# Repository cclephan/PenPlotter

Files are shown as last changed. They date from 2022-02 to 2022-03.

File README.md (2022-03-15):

# Pen Plotter
## Date Updated: March 15, 2022
## Christian Clephan, Kyle McGrath
### Introduction

Our device was a 2.5 axis pen plotter, capable of taking in HPGL files as input and drawing on a piece of paper as the output. For our device we used polar coordinates. A radial arm moving around a hub was used to create the changes in angle, and the pen was moved radially using a rail system with a belt to provide the radial motion. The remaining 0.5 axis is the moving of the pen up and down. 

The device was intended to be used by its two creators: Christian Clephan and Kyle McGrath to demonstrate their mechatronics knowledge in the Term Project. Our goal was to create a robot which could draw anything, which we were able to accomplish by drawing some parallel lines, arcs, and scripples in the formation of a rectangle.

### Hardware Design Overview
Our Pen Plotter has two degrees of freedom controlled by two Pittperson DC motors and the half degree of freedom controlled by 1 servo motor. The servo motor controls the up and down motion of the pen by swinging in an arc downwards and perpendicular to the page, or upwards and parallel (not touching the page). One of the DC motors controls the radial motion of the pen plotter by spinning a timing belt, while housed on the rotational base. The timing belt fits around the motor gear and pulley wheel on the opposite side, which moves a carriage holding the servo motor and pen. The carriage rests on two metal rods which allow it to freely move in the radial direction. The angular direction is controlled by the other DC motor spinning the base holding the plotter. A wheel was attached to the other end of the plotter to allow for rotation as the motor spun the entire system. The spinning base, wheel, carriage, and radial motor housing were all 3D printed. Other materials such as the rods, pulley wheel, and fasteners were found in the lab scrap bin, while the timing belt was purchased from McMaster-Carr. Detailed drawings and CAD models of the hardware can be found at https://github.com/cclephan/PenPlotter/tree/main/PenPlotterModel.

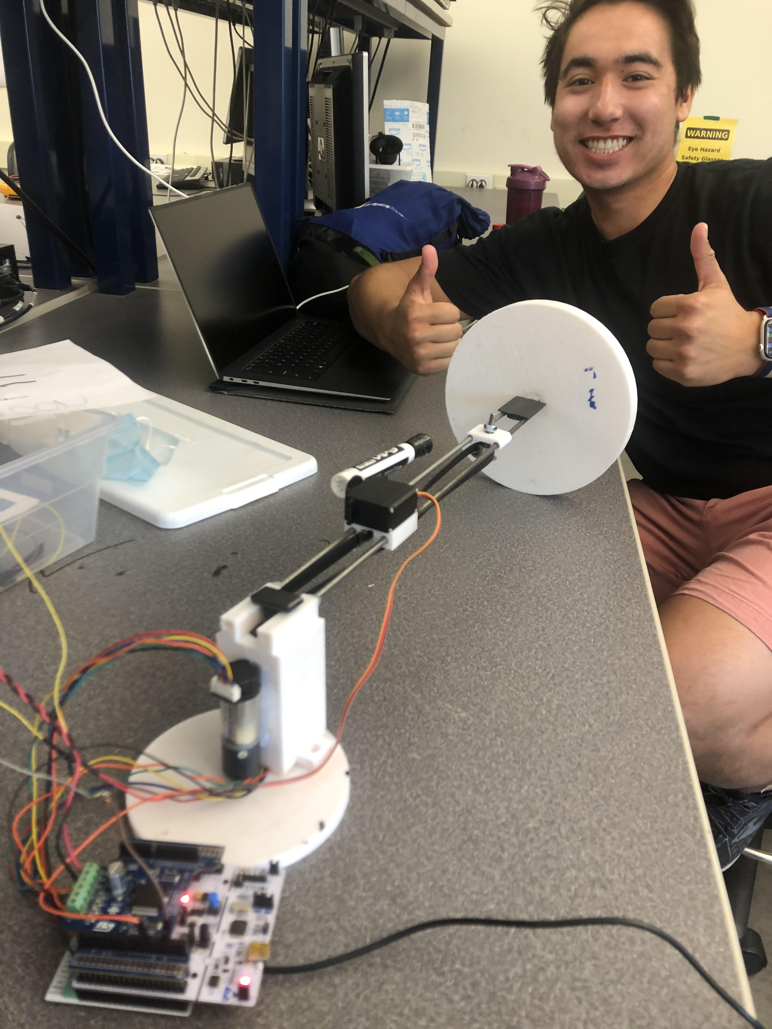
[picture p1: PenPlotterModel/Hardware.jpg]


Figure 1: Pen Plotter Hardware

### Software Design Overiew
Link to Doxygen for futher software design details: https://cclephan.github.io/PenPlotter/

The software consisted of utilizing several of our old files used in previous ME 405 labs as well as some new files to manage the HPGL processing. 

The files that were reused from previous labs were the Closed Loop Controller File, the Motor Driver File, and the Encoder Reader File. 

The parsing file would open the respective HPGL file and convert the HPGL coordinates into two rotational commands that are inputted into the closed loop controller file. HPGL coordiantes were provided in X and Y coordinates, these were converted to Polar Coordiantes using Trigonometry. The radial coordinate was then converted to a second theta coordinate for the motor driving the radial motion. 

The servo driver file was also new and included creating a timer, timer channel, and two functions which applied a PWM signal turning the servo motor so the pen is either up or down.

Our Task Diagram for the whole system can be seen in the Doxygen page. Some of the organization for the tasks have changed since the proposal, but this was due to hardware and time limitations. 

### Results
Our system came close to drawing what was inputted from the HPGL file, but there were still several shortcomings. Our most successful attempt was an attempt to draw two parallel lines, a video of which can be seen below. 

We tested our system by providing HPGL inputs and printing the respective commands provided to the motors. We then performed hand calculations to confirm that the commands provided to the motors match what we wanted to do. Initially we noticed that the commands that were provided to the motors did not match the hand calculations that we performed. We believed this was due to our use of Queues as we were saving our commands as integers instead of floats. We changed this and the inputs to the motors more closely followed desired results. 

The first HPGL file that we tested with our system was a straight line that was drawn in Inkscape and exported as an HPGL. One of earlier tests with drawing two straight lines can be seen here: https://youtu.be/u9vNNVAs_34. After taking some time to modify the speed of each motor and the period associated with each task, we eventually were able to draw two parallel lines. The video of drawing two parallel lines can be seen here: https://youtube.com/shorts/n7fFq1dV0Q4?feature=share. Some of our later tests that were unsuccessful were attempts to draw rectangles or circles. A failed rectangle attempt can be seen here: https://youtu.be/5r2_hMjXv8Q. We believe our system could have failed these tests because we did not interpolate between points which could have allowed for more defined motion between the points. We also struggled with finding a good condition statement to move to the next setpoint value once the motor has reached it's desired point. We tried to use a condition to see if the encoder position was close to the setpoint value, but it was hard to tune the controller for that condition, especially with the low resolution in our hardware design.

### What we learned
What worked well for this pen plotter was obtaining the hardware we needed and creating models that could be easily 3D printed and assembled. We noticed other groups struggled obtaining and purchasing materials, while most of our parts could be printed or found in the scrap bin. We were also able to complete tests to see how our motors moved the system around to ensure the hardware functioned as intended in the design. However, from this project we learned the importance of testing our code early and often. We made the mistake of believing the software portion of our project wouldn't be too complicated as we planned to reuse several files from older projects. We ran into some difficulty getting all the commands from the HPGL file to read as sometimes commands would get skipped over. We eventually learned this was likely due to either calling queue.read() twice as well as cotask running tasks either too quick or slow. There were other errors that we were unable to fix and from this we learned to not underestimate how long the software portion of a project will take. We also learned the importance of designing for as much resolution as possible in the hardware design, so controlling the motors in software would be much easier. Our rotational motor only had 1/4 revolution of a turn in resolution, which made positional control for complex shapes practically impossible. Sticking to a direct drive shaft attached to a smaller wheel would have been a much smarter choice as shown in the original example. 

Another thing we learned is the importance of using states in our code. We believed it would be easier to create code that works first and then implement the states after we had code that worked. In the end our code did not work as expected and we decided it was time to update the code to utilize states. We quickly saw that by using states, readability of the code improved significantly, and we were able to easily spot errors that we had missed. 

In the future we would recommend investigating interpolating the HPGL commands so there isn't as much noise. We would also recommend using direct drive for spinning a small wheel, therefore there is more resolution for position control. Finally, implementing finite states machines for each task early on would improve overall code readability and allow for quick code diagnosing. 

### Additional files 
Detailed CAD be found at: https://github.com/cclephan/PenPlotter/tree/main/PenPlotterModel

Two Line Video Attempt 1: https://youtu.be/u9vNNVAs_34

Two Line Video Succesful: https://youtube.com/shorts/n7fFq1dV0Q4?feature=share

Rectangle Video: https://youtu.be/5r2_hMjXv8Q

# Pen Plotter Proposal
## Date Updated: Feb 17, 2022 
## Christian Clephan, Kyle McGrath
### Description

Our proposed design will utilize a radial arm rotating around a hub. In the top right corner of the piece of paper will be a 3D rotating hub 
driven by a Pittperson Gearmotor. The gearmotor will provide torque to our radial arm which will consist of a rail system on which a flat bracket carrying the pen is mounted. The rail system will consist of metal tubes that we hope to find around the Aero Hanger and will be supported by 3D printed brackets (translational hub). The pen carrying bracket will be moved translationally by a belt. The belt will be obtained from McMaster-Carr and it will also be driven by a Pittperson Gearmotor. At the end of the rail system, we will mount a wheel in order to allow for free rotation of the system. At the end of the translational belt system there will be a platform to hold a gear, and on the other side a rod connecting to the free moving wheel. The wheel will likely be a hobby wheel for RC cars that we will obtain from Zacsters, or 3D printing could be an option. The pen carrier will be raised and lowered using an SG90 servo obtained from Zacsters. All parts with complex geometry or of small size will likely be 3D printed at Mustang 60. 

For our rail system, we want the rails to extend past the diameter of the paper in order to prevent the wheel from disrupting or damaging the paper. The rails will provide a fixed length between the motor and the wheel while also allowing the pen to move freely back and forth. All components, assembly, and drawing can be found in PenPlotterModel folder of this repository. Below is an drawing of our assembly with some dimensions (belt is not pictured, but would run between two translational gears).

One possible concern with our design is if the provided Pittperson Gearmotors can provide enough torque to drive the radial arm rails. Another concern of ours is implementing the rails to drive the pen radial motion as this is something we are both inexperienced with. 

Table 1. Bill of Materials

| Qty. | Part | Source | Est. Cost |
|:----:|:---|:---|:---:|
|  2 | Pittperson Gearmotors | ME405 Tub | - |
|  1 | Nucleo with Shoe | ME405 Tub | - |
|  1 | Purple Sharpie | Home supply | - |
|  1 | SG90 Servo | Zacsters | $1.50 |
|  3 | Metal Rods | Aero Hanger Trash | - |
|  1 | 3D Printed Translation Hub | Mustang 60 | - |
|  1 | RC Hobby Wheel | Zacsters | $3.00 |
|  1 | Belt | McMaster-Carr |  $10.43 |
|  1 | 3D Printed Pen Holder | Mustang 60 | - |
|  1 | Rotation Hub | Mustang 60 | - |
|  1 | Gear/Platform for Translation | Mustang 60 | - |

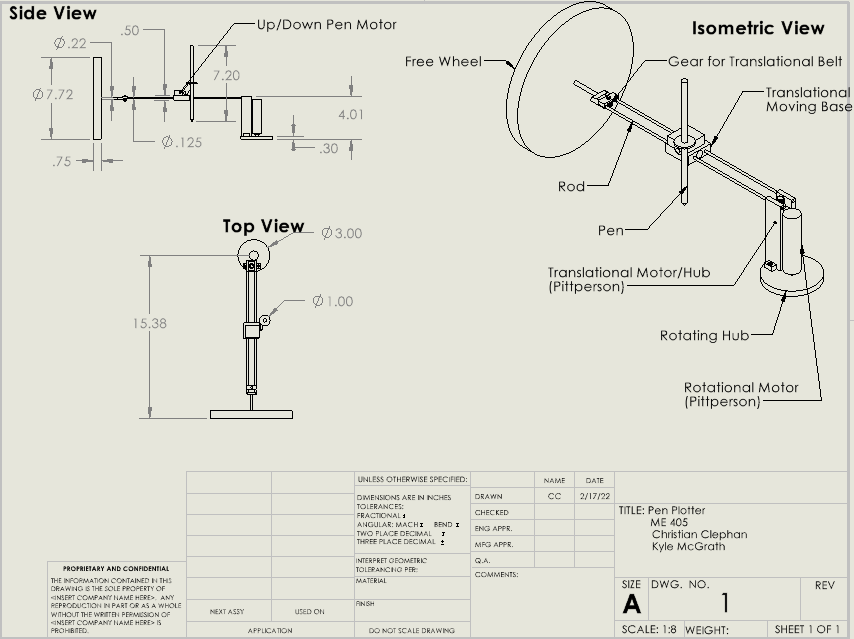
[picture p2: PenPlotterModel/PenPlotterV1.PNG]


Figure 1. Detailed Drawing of Pen Plotter Assembly

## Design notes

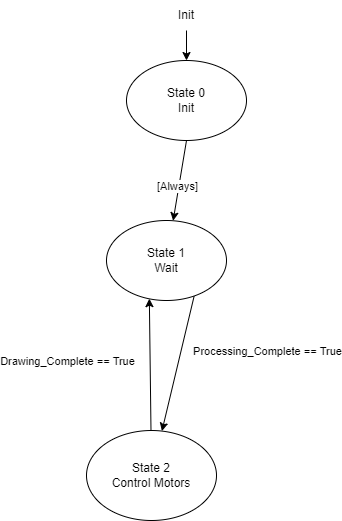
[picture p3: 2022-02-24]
docs/Controller_Task.png

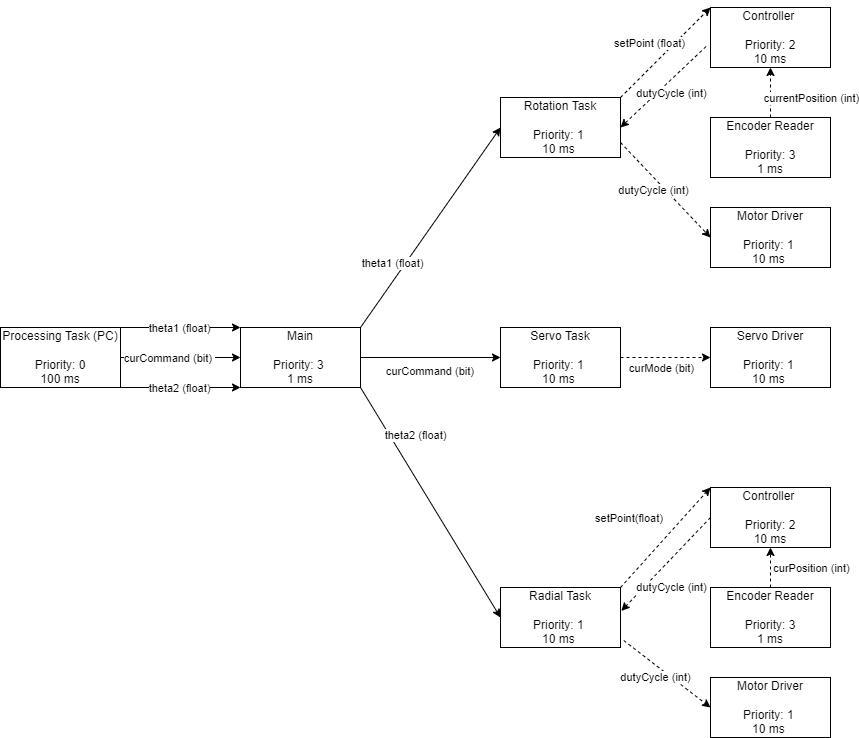
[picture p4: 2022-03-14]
docs/UpdatedTaskDiagram.png

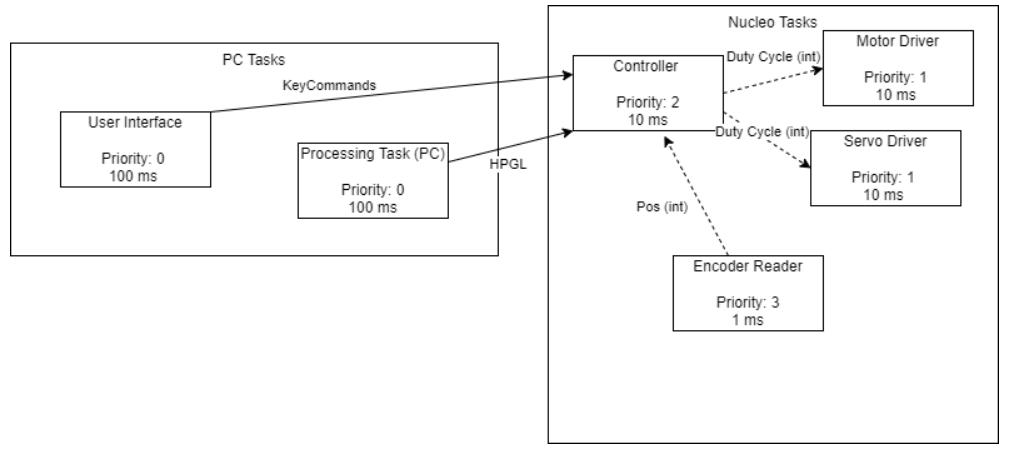
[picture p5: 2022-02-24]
docs/TaskDiagram.png

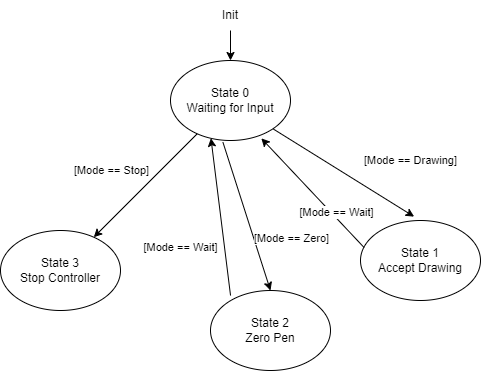
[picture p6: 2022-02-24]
docs/UI_Task.png

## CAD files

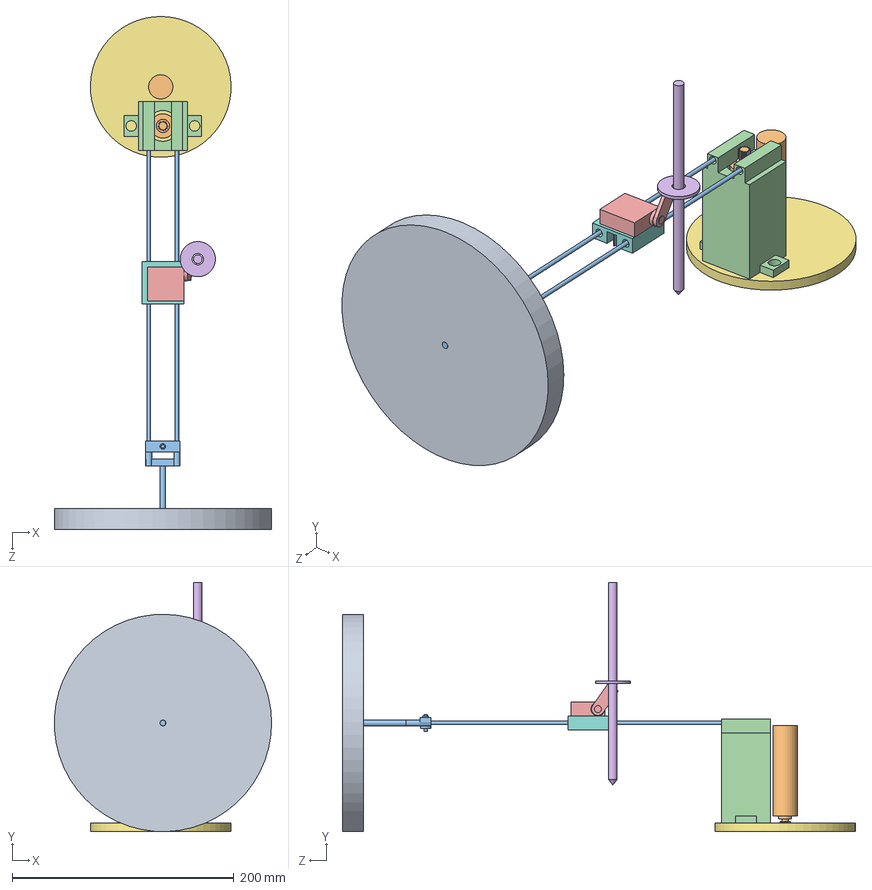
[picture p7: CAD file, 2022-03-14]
PenPlotterModel/Proto Pen Plotter.SLDASM
196.0 x 224.9 x 462.9 mm
Free Spinning Wheel
Pittman Motor x 2
Rod
Translational Motor Hub
2941 Mini Motor
Pencil Holder
Rotation Hub
Translational Moving Base

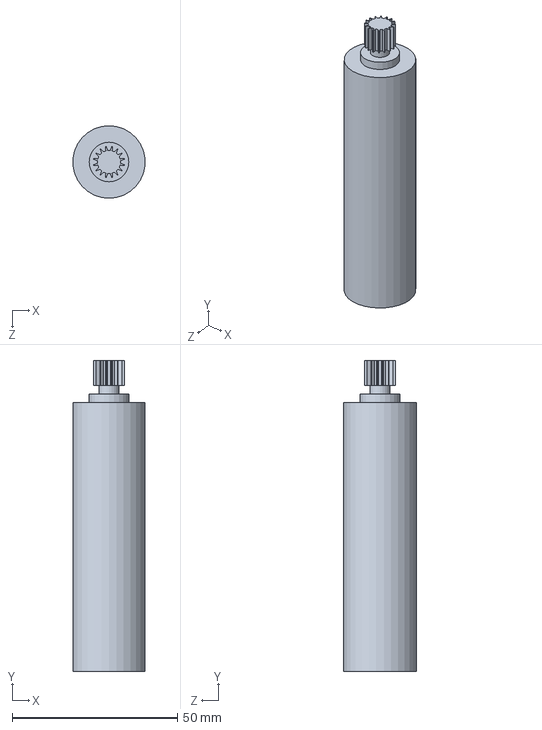
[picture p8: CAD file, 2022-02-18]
PenPlotterModel/Pittman Motor.SLDPRT
21.9 x 94.2 x 22.0 mm

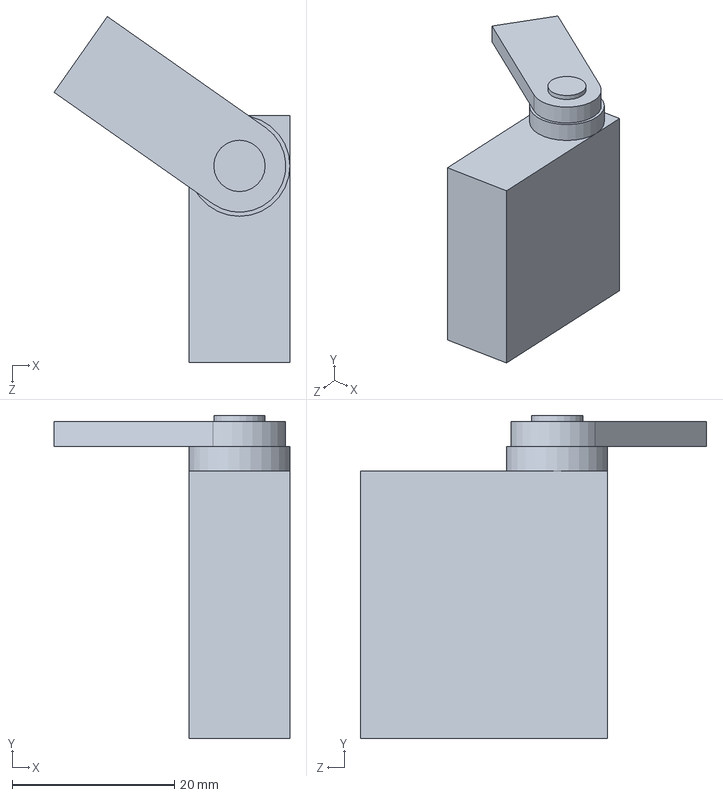
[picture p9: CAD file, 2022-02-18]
PenPlotterModel/2941 Mini Motor.SLDPRT
29.1 x 39.9 x 42.7 mm

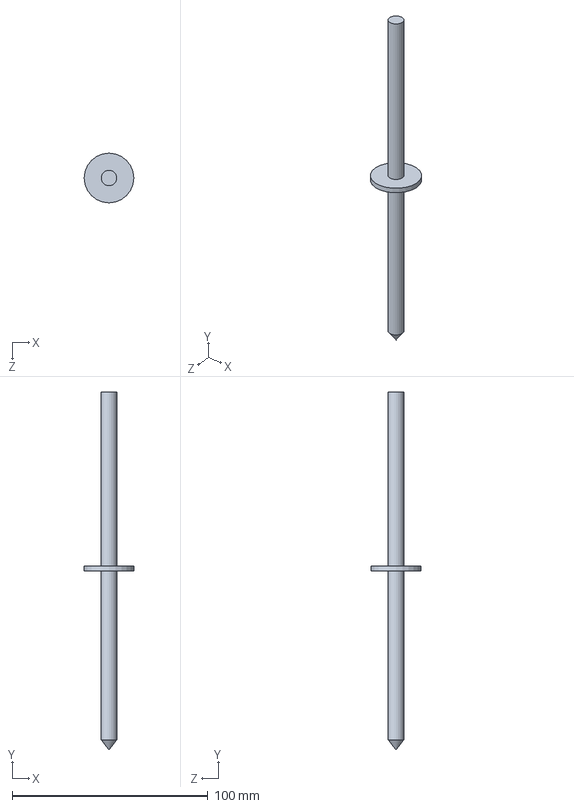
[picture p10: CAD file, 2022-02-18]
PenPlotterModel/Pencil Holder.SLDPRT
25.4 x 183.0 x 25.4 mm

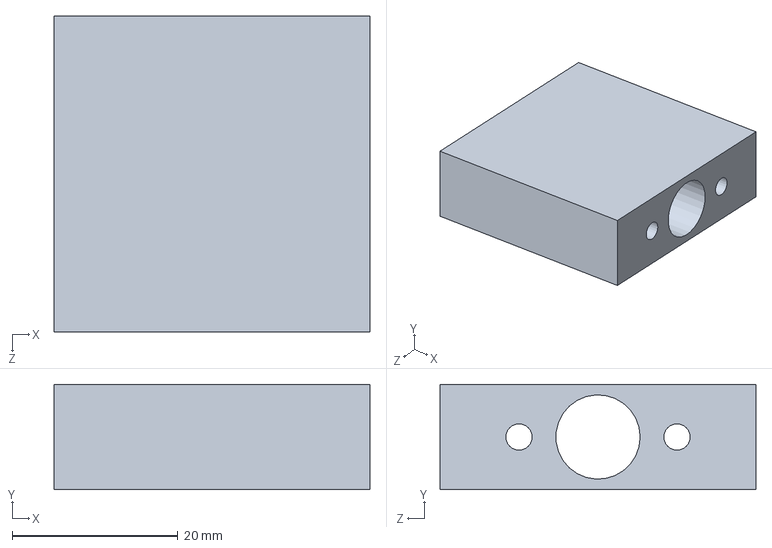
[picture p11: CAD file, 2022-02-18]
PenPlotterModel/Translational Moving Base.SLDPRT
38.1 x 12.7 x 38.1 mm

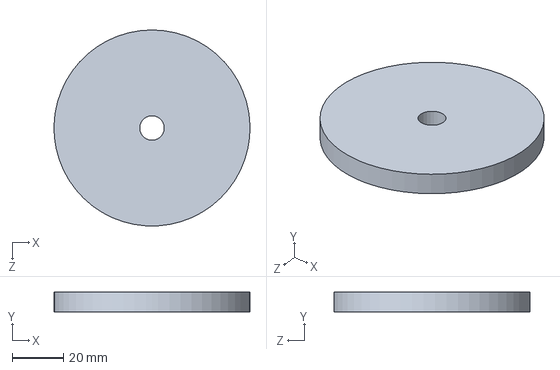
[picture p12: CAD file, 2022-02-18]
PenPlotterModel/Rotation Hub.SLDPRT
76.2 x 7.62 x 76.2 mm

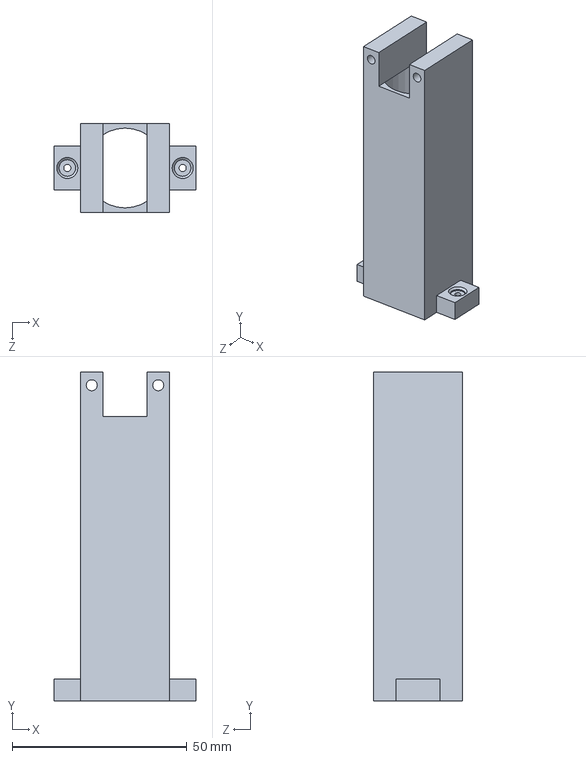
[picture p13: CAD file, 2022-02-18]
PenPlotterModel/Translational Motor Hub.SLDPRT
40.6 x 94.2 x 25.4 mm

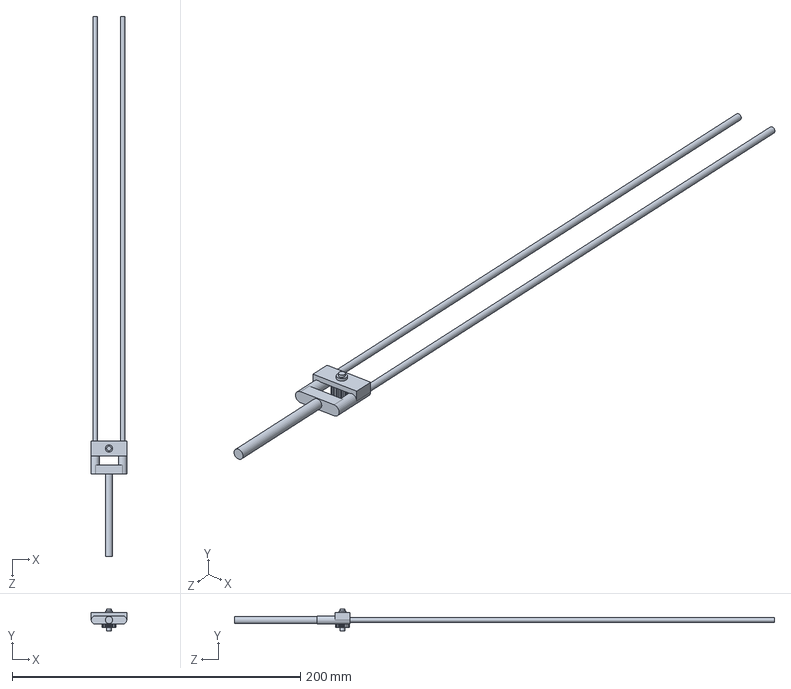
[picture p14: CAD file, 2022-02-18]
PenPlotterModel/Rod.SLDPRT
24.7 x 15.2 x 374.6 mm

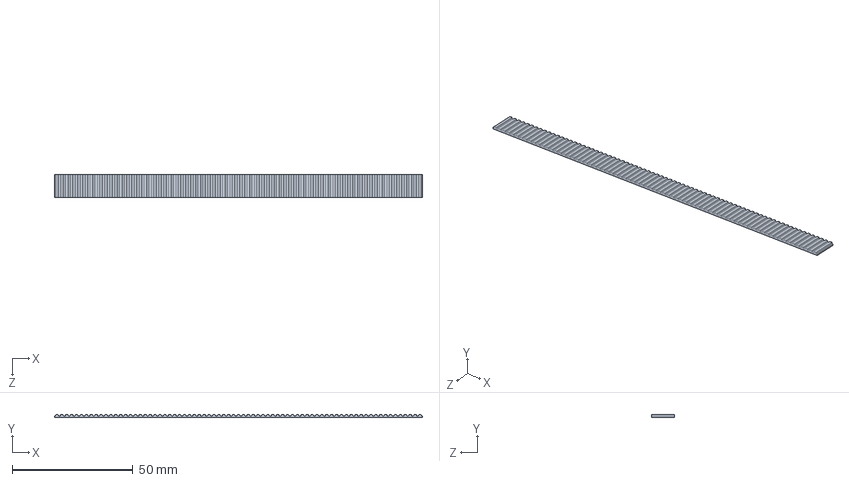
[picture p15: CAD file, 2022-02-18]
PenPlotterModel/Belt.SLDPRT
152.4 x 1.14 x 9.53 mm

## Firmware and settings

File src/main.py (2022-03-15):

"""!
@file main.py
Main file for pen plotter robot which is run by the user. The program begins by creating state variables,
queues, and asking the user for HPGL filename. Once the user inputs the filename, our data collection task
is run to put all the setpoint values for respective radial/angular/and servo motor into queues. The task
functions for each motor are then created as objects using cotask and appended to a list. This list is then
continuously run until there are no setpoint values left in each queue. Finally, the motors are turned off
and a print statement lets the user know the program is over.
@author Christian Clephan
@author Kyle McGrath
@date   02-Jan-2022
@copyright (c) 2022 released under CalPoly
"""
import math
import pyb
import cotask
import gc
import control
import utime
import encoder_clephan_mcgrath
import motor_clephan_mcgrath
import servo_driver
import task_share

##Ticks
ticks_per_rev = 256*2*16
r = 0.375/2 #in

def task_data_collect():
    '''!
    @brief Collects X/Y data from HPGL drawing and converts into readable commands for rotational/radial/servo motors
    @details Opens file specified by the user and converts HPGL standard commands to readable code to be put in
    a queue and read by other tasks as setpoint values for motor control. X/Y coordinates are converted to polar
    coordinates in revolutions for respective motors to spin. Finally, the setpoints in revolutions for DC motors
    and up or down commands for pen are put into their resepctive queues.
    '''    
    state = 0
    if state == S0_DATA_INIT:
        x_commands = []
        y_commands = []  
        theta_commands = []
        ##Dots per inch as specified by inkscape when creating drawing.
        dpi = 1016 
        state = S1_COLLECT_DATA
    if state == S1_COLLECT_DATA:    
        with open(file_name) as file:
            commands= []
            for line in file.readlines():
                currentLine = line.split(";")
                for thing in currentLine:
                    test = thing.split(',')
                    if ("PD" in test[0] or "PU" in test[0]) and len(test[0]) > 2:
                        if "PD" in test[0]:
                            test[0] = test[0][2:]
                            test.insert(0, "PD")
                        elif "PU" in test[0]:
                            test[0] = test[0][2:]
                            test.insert(0, "PU")
                    commands.append(test)
        state = S2_CONVERT_DATA
    
    if state == S2_CONVERT_DATA:
        for command in commands:
            i = 1
            if command[0] == "PU":
                cur_command = 0
            elif command[0] == "PD":
                cur_command = 1
            while i < len(command):
                ##X coordinate of HPGL command
                x_var = float(command[i])/dpi #inch
                x_commands.append(x_var)
                i = i + 1
                ##Y coordinate of HPGL command
                y_var = float(command[i])/dpi
                y_commands.append(y_var)          
                if x_var != 0:
                    ##Converted X/Y coordinate to rotational setpoint in revolutions
                    theta1 = math.atan(y_var/x_var) / (2*math.pi)
                else:
                    theta1 = 0
                i = i + 1
                radial = math.sqrt(x_var**2 + y_var**2)
                ##Converted X/Y coordinate to radial setpoint in revolutions
                theta2 = radial/(r*2*math.pi)
                q_theta_rot.put(theta1)
                q_theta_rad.put(theta2)
                q_servo.put(cur_command)
        
def stop_motors():
    '''!
    @brief Stops rotational and radial motors; used at the end of main.py program.
    '''
    pinA10 = pyb.Pin(pyb.Pin.board.PA10, pyb.Pin.OUT_PP)
    pinB4 = pyb.Pin(pyb.Pin.board.PB4)
    pinB5 = pyb.Pin(pyb.Pin.board.PB5)
    pinC1 = pyb.Pin(pyb.Pin.board.PC1, pyb.Pin.OUT_PP)
    pinA0 = pyb.Pin(pyb.Pin.board.PA0)
    pinA1 = pyb.Pin(pyb.Pin.board.PA1)
    motor_rot = motor_clephan_mcgrath.MotorDriver(pinC1, pinA0, pinA1, 5)
    motor_rad = motor_clephan_mcgrath.MotorDriver(pinA10, pinB4, pinB5, 3)
    
    motor_rot.set_duty_cycle(0)
    motor_rad.set_duty_cycle(0)

def task_rot_motor():
    '''!
    @brief Rotational motor task drives the motor to specified setpoint and repeats the process with new setpoints until there are none left
    @details First the rotational motor/encoder pins are initialized and created as objects along with a controller.
    Next, the encoder is zeroed and a timer is started for which a motor will be driven to a setpoint by a controller
    which constantly updates and sends duties to the motor based on position control. After 1 second another setpoint
    value is given to the controller for which the motor is driven again. This is repeated until there are no setpoint
    values left in the queue and the motor is stopped.
    '''
    state = 0
    if state == S0_INIT:
        start = True
        pinC1 = pyb.Pin(pyb.Pin.board.PC1, pyb.Pin.OUT_PP)
        pinA0 = pyb.Pin(pyb.Pin.board.PA0)
        pinA1 = pyb.Pin(pyb.Pin.board.PA1)
        ##Rotational motor object created using motor driver file from previous lab
        motor_rot = motor_clephan_mcgrath.MotorDriver(pinC1, pinA0, pinA1, 5)
        
        pinC6 = pyb.Pin(pyb.Pin.board.PC6)
        pinC7 = pyb.Pin(pyb.Pin.board.PC7)
        ##Rotational encoder object created using encoder driver file from previous lab
        encoder_rot = encoder_clephan_mcgrath.Encoder(pinC6,pinC7,8)
        ##Current motor position
        current_position = 0
        ##Last motor position used to calculated difference between current and last for the next setpoint
        last_position = 0
        ##Rotational controller object created using controller file from previous lab
        controller_rot = control.ClosedLoop([.15,0,0], [-100,100], ticks_per_rev* current_position)
        state = S1_START
    while state != S4_STOP:

        if state == S1_START:
            #State 1 zeros encoder and starts initial and current timer
            encoder_rot.zero()
            startTime = utime.ticks_ms()
            t_cur = utime.ticks_ms()
            state = S2_DRIVE_MOTOR
            
        if state == S2_DRIVE_MOTOR:
            #State 2 updates encoder position for duty cycle to be calculated by controller and sent over to motor
            encoder_rot.update()
            t_cur = utime.ticks_ms()
            duty = controller_rot.update(encoder_rot.read(), startTime)
            motor_rot.set_duty_cycle(duty)
            if t_cur >= startTime+1000:
                state = S3_CHANGE_SETPOINT
        if state == S3_CHANGE_SETPOINT:
            #State 3 changes the setpoint of the motor with the next queue value from data collection
            startTime = t_cur
            if q_theta_rot.any():
                last_position = current_position
                current_position = q_theta_rot.get()
                ##Next rotational setpoint value in revolutions
                new_set_rot = current_position - last_position
                print('Rotation ticks: ' + str(ticks_per_rev*new_set_rot))
                controller_rot.set_setPoint(ticks_per_rev* new_set_rot)
            if q_theta_rot.empty():
                state = S4_STOP
            else:
                state = S2_DRIVE_MOTOR
        if state == S4_STOP:
            print('Stopping rot')
            motor_rot.set_duty_cycle(0)
        yield (0)


def task_rad_motor():
    '''!
    @brief Radial motor task drives the motor to specified setpoint and repeats the process with new setpoints until there are none left
    @details First the radial motor/encoder pins are initialized and created as objects along with a controller.
    Next, the encoder is zeroed and a timer is started for which a motor will be driven to a setpoint by a controller
    which constantly updates and sends duties to the motor based on position control. After 1 second another setpoint
    value is given to the controller for which the motor is driven again. This is repeated until there are no setpoint
    values left in the queue and the motor is stopped.
    '''
    state = 0
    if state == S0_INIT:
        pinA10 = pyb.Pin(pyb.Pin.board.PA10, pyb.Pin.OUT_PP)
        pinB4 = pyb.Pin(pyb.Pin.board.PB4)
        pinB5 = pyb.Pin(pyb.Pin.board.PB5)
        ##Radial motor object created using motor driver file from previous lab
        motor_rad = motor_clephan_mcgrath.MotorDriver(pinA10, pinB4, pinB5, 3)

        pinB6 = pyb.Pin(pyb.Pin.board.PB6)
        pinB7 = pyb.Pin(pyb.Pin.board.PB7)
        ##Radial encoder object created using encoder driver file from previous lab
        encoder_rad = encoder_clephan_mcgrath.Encoder(pinB6,pinB7,4)
        
        ##Current radial motor position
        current_rad = 0
        ##Last radial motor position used to calculated difference between current and last for the next setpoint
        last_rad = 0
        ##Radial controller object created using controller file from previous lab
        controller_rad = control.ClosedLoop([.11,0,0], [-100,100], ticks_per_rev*current_rad)
        state = S1_START
        
    while state != S4_STOP:
        if state == S1_START:
            #State 1 zeros encoder and starts initial and current timer
            encoder_rad.zero()
            startTime = utime.ticks_ms()
            t_cur = utime.ticks_ms()
            state = S2_DRIVE_MOTOR
            
        if state == S2_DRIVE_MOTOR:
            #State 2 updates encoder position for duty cycle to be calculated by controller and sent over to motor
            encoder_rad.update()
            t_cur = utime.ticks_ms()
            duty = controller_rad.update(encoder_rad.read(), startTime)
            motor_rad.set_duty_cycle(duty)
            print('Changing duty')
            if t_cur >= startTime+1000:
                state = S3_CHANGE_SETPOINT
        if state == S3_CHANGE_SETPOINT:
            #State 3 changes the setpoint of the motor with the next queue value from data collection
            startTime = t_cur                
            if q_theta_rad.any():
                last_rad = current_rad
                current_rad = q_theta_rad.get()
                ##Next radial setpoint value in revolutions
                new_set_rad = current_rad - last_rad
                print('Radial ticks: ' + str(ticks_per_rev*new_set_rad))
                controller_rad.set_setPoint(ticks_per_rev*new_set_rad)
            if q_theta_rad.empty():
                state = S4_STOP
            else:
                state = S2_DRIVE_MOTOR
        if state == S4_STOP:
            print('Stopping rad')
            motor_rot.set_duty_cycle(0)
        yield (0)


def task_servo():
    '''!
    @brief Sends a PWM signal to the servo to make the pen go up or down based on whether the converted HPGL command is a 1 or 0
    '''
    state = 0
    if state == S0_SERVO_INIT:
        pinA7 = pyb.Pin(pyb.Pin.board.PA7,pyb.Pin.OUT_PP)
        pinA10 = pyb.Pin(pyb.Pin.board.PA10, pyb.Pin.OUT_PP)
        ##Servo object created with driver file
        servo = servo_driver.ServoDriver(pinA10,pinA7,3)
        ##Current mode that is sent by q_servo
        curMode = 0
        state = S1_PEN_UP
    while q_servo.any():
        curMode = q_servo.get()
        if curMode == 0 and state == S2_PEN_DOWN:
            #Moves pen up
            servo.pen_up()
            state = S1_PEN_UP
        elif curMode == 1 and state == S1_PEN_UP:
            #Moves pen down
            servo.pen_down()
            state = S2_PEN_DOWN
        yield (0)
    
if __name__ == '__main__':
    
    #State variables for task_data_collect FSM
    S0_DATA_INIT = 0
    S1_COLLECT_DATA = 1
    S2_CONVERT_DATA = 2
    
    #State variables for motor tasks FSM
    S0_INIT = 0
    S1_START = 1
    S2_DRIVE_MOTOR = 2
    S3_CHANGE_SETPOINT = 3
    S4_STOP = 4
    
    #State variables for servo task FSM
    S0_SERVO_INIT = 0
    S1_PEN_UP = 1
    S2_PEN_DOWN = 2
    
    #Creating Queues
    q_theta_rad = task_share.Queue ('f', size = 400, thread_protect = False, overwrite = False,
                           name = "Queue Theta Radial")
    q_theta_rot = task_share.Queue ('f', size = 400, thread_protect = False, overwrite = False,
                           name = "Queue Theta Rotational") 
    q_servo = task_share.Queue ('b', size = 400, thread_protect = False, overwrite = False,
                           name = "Queue Servo")
    
    #Asks user for HPGL File
    file_name = input('Enter HPGL filename: ')
    
    #Runs Data Collection task
    task_data_collect()
    print('Data Collection Finished')
    

    #Creating task objects
    task_rot = cotask.Task (task_rot_motor, name = 'Task Rotational Motor', priority = 1, 
                         period = 500, profile = True, trace = False)
    task_rad = cotask.Task (task_rad_motor, name = 'Task Radial Motor', priority = 1, 
                         period = 500, profile = True, trace = False)
    task_srvo = cotask.Task (task_servo, name = 'Task Servo', priority = 0, 
                     period = 500, profile = True, trace = False)
    
    cotask.task_list.append (task_rot)
    cotask.task_list.append (task_rad)
    cotask.task_list.append (task_srvo)
    gc.collect ()
    
    #Running Cotask with task objects
    while q_servo.any():
     try:
         cotask.task_list.pri_sched ()
     except KeyboardInterrupt:
        break
    
    #Cuts off motors
    stop_motors()
    
    print('Program over')

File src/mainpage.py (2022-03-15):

"""!
@file mainpage.py
This file contains information regarding software design
@author Christian Clephan
@author Kyle McGrath
@date   15-Mar-2022
@copyright (c) 2022 released under CalPoly

@mainpage

@section sftware Software Design
            This section includes information regarding our pen plottor robot
            software design. Below in Figure 1 is a task diagram of all information that
            will be shared between tasks to accomplish our goal. To operate the robot, the user 
            will run the main file and input an HPGL file that will be processed. The main file 
            will then call the Processing Task which will place the current command (Pen Up or Pen Down) 
            and the theta positions in revolutions that will be input to the radial, rotational,
            and servo tasks. The servo task will output a 0 or a 1 to the servoDriver based on 
            whether the Pen needs to be UP (1) or DOWN (0). 
            The radial and rotational tasks will output the setPoint in ticks
            to the controller task which calls the encoder task to calculate a duty cycle 
            based on the proportional gain and encoder read values. 
            This duty cycle is then input into the motor driver task to drive the motor. <br>
            \image html UpdatedTaskDiagram.png "Figure 1: Squiggly Task Diagram" <br>
            
            The previous Task Diagram could also be seen below in Figure 2. Some changes 
            that we made are that we opted to have all the processing performed on the Nucleo, 
            and we decided to have the User Interface built into the main file. 
            \image html TaskDiagram.png "Figure 2: Previous Task Diagram" <br>

@subsection task_process Processing Task
            Once the user has input a drawing the processing task will convert
            the drawing to X and Y coordinates. From those X and Y coordinates,
            inverse kinematics will be used to translate X/Y to theta 1 and theta 2 motor positions in revolutions. 
            This information is then added to two different queues and sent to either the Rotation 
            or Radial tasks. A third queue called curCommand is also filled. This queue contains bits
            with the command Pen up (1) or Pen down (0). The curCommand queue is sent to the servo task <br>
            
            \image html Parse_Task.png "Figure 3: Processing Task FSM" <br>

@subsection task_rotation_radial Rotation and Radial Task
            The rotation and radial tasks control the respective motor drivers, controllers, 
            and encoders related to each motor. The rotation and radial task perform 
            exactly the same so both will be described here. Once the theta 1 and theta 2
            positions are in their respective queues, the desired setPoint in ticks is sent to the controller 
            task. The controller task then calls the Encoder Reader to get the current position 
            and returns a desired duty cycle to the rotation/radial task. This duty cycle 
            is then inputted into the motor driver task. <br> 
            
            \image html Rotation_Radial_Task.png "Figure 4: Rotational and Radial Task FSM" <br>
            
@subsection task_servo Servo Task
            Servo task will initiate and alternate between two states: Pen Up or 
            Pen Down depending on the desired command put in the curCommand queue. 
            The desired mode is then sent to the servo driver. <br>
            
            \image html Servo_Task.png "Figure 5: Servo Task FSM" <br>

@subsection task_controller Controller Task
            Task controller will wait for a provided setPoint from the Rotation or Radial Tasks
            and use path data with a proportional gain input to send PWM
            signals to respective motors tasks. <br>
            
            \image html Controller_Task.png "Figure 6: Controller Task FSM" <br>

@subsection motor_driver Motor Driver
            Task motor driver will recieve PWM duty cycles from the rotation or radial tasks
            and apply the signal to instantiated motors. <br>
            
@subsection servo_driver Servo Driver
            Task servo driver will receive curMode commands from the servo task 
            and apply the signal to the servo. <br> 
            

@subsection task_encoder Encoder Reader
            Task encoder will be the highest priority, constantly sending
            motor positions for radial and angular motors. Task controller will
            receive these values and interpret them to vary PWM for motors.<br>
            
            
"""

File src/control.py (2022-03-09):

"""!
@file control.py
Closed loop controller containing methods to control an arbitraries motor duty cycle 
@author Christian Clephan
@author Kyle McGrath
@date   02-Jan-2022
@copyright (c) 2022 released under CalPoly
"""

import utime


class ClosedLoop:
    '''!
    @brief                  Interface with closed loop controller
    @details                Contains all methods that will be used in task_hardware to set the duty cycle based on closed
                                loop control.
    '''
        
    def __init__ (self,PID, satLim, setPoint):
        '''!
        @brief Constructs a closed loop controller
        @details Creates variables necessary to instantiate a controller such as timing, PID gains, saturation
        limit, setpoint value, error, and arrays used in recording a step response
        @param PID is a list containing the three gain values for Kp/Ki/Kd
        @param satLim is a list containing the upper and lower bounds of saturation      
        '''
        ## @brief Instantiates PID controller with gains
        self.firstTime = 0
        self.i = True
        self.PID = PID
        # PID Kp(*%/rad)Ki(*%/rad)Kd(*%s2/rad)
        ## @brief Instantiates duty saturation upper and lower bounds
        self.satLim = satLim
        
        self.setPoint = setPoint
        
        ## @brief Sum of error over a difference in time
        self.esum = 0
        ## @brief Previous error
        self.laste = 0
        self.times = []
        self.motorPositions = []
        #self.t0 = utime.ticks_ms()
        
        #print("Controller Instantiated")

    def update (self, Read, startTime):
        '''!
        @brief Updates the controller for timing and error between a read value and the setpoint
        @param Read is the value returned by the sensor detecting the current state of the system (encoder position)
        @param startTime is the initial time for a step response.    
        @return Sends back saturated duty value using sat method.
        '''
        ## @brief Error signal which is the difference between a reference and input (current) value.
        tcur = utime.ticks_ms()
        tdif = utime.ticks_diff(tcur,startTime)
        if self.i:
            self.firstTime = tdif
            self.i = False
        self.times.append(tdif-self.firstTime)
        self.motorPositions.append(Read)
        e = self.setPoint - Read
        #Updates sum of error (area under curve)
        # self.esum += (self.laste+e)*tdif/2
        # ## @brief Delta error calculated by taking difference in error values over a time difference
        # dele = (e - self.laste)/tdif
        # # Updates last error
        # self.laste = e
        #print(e)

        
        ## @brief Duty calculation using PID gains and error values
        # duty = self.PID[0]*(e) + self.PID[1]*(self.esum) + self.PID[2]*(dele) 
        duty = self.PID[0]*(e)
        #print(self.motorPositions)
        return duty
        #return self.sat(duty)
                
                
    def get_Times(self):
        '''!
        @brief Returns time array for a step response
        @return Contains array of time over a step response
        '''
        return self.times
    
    def getPositions(self):
        '''!
        @brief Returns motor positions array for a step response
        @return Contains encoder read positions of a motor over a step response
        '''
        return self.motorPositions
    
    def get_PID(self):
        '''!
        @brief Gets PID object
        @details Quick method to determine what controller is using for PID gains.     
        '''
        return self.PID
    
    def set_PID(self, PID):
        '''!
        @brief Sets PID gains.
        @details Sets PID gains to some new list of values for Kp/Ki/Kd 
        @param PID is a list containing the three gain values for Kp/Ki/Kd    
        '''
        self.PID = PID
        
    def set_setPoint(self,setPoint):
        '''!
        @brief Sets or resets setpoint to a certain value
        '''
        self.setPoint = setPoint
        
    def sat(self,sat_duty):
        '''!
        @brief Saturation functionallity
        @details Controls if a duty is too large from what is calculated in update method.
        @param sat_duty is the value sent by what is calculated in update method.
        @return Sends back either the saturated limit if duty is too high or original duty based on bounds.
        '''
        if sat_duty<self.satLim[0]:
            return self.satLim[0]
        elif sat_duty>self.satLim[1]:
            return self.satLim[1]
        return sat_duty
      

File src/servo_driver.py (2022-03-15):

"""!
@file servo_driver.py
This file contains the ServoDriver Class used to drive MG 996R servo with pen up/down methods
@author Christian Clephan
@author Kyle McGrath
@date   03-March-2022
@copyright (c) 2022 released under CalPoly
"""

import pyb

class ServoDriver:
    """! 
    This class implements a MG 996R servo.
    """
    def __init__(self,en_pin,pwm_pin,timer):
        """! 
        @brief Instantiates servo object by setting enable pin to high and creating timer/timer channel objects for PWM control
        @param en_pin is the enable pin for the servo motor
        @param pwm_pin is the PWM pin used on Nucleo to send signal
        @param timer is the timer number used corresponding to PWM pin
        """
        en_pin.high()
        ##50Hz timer at specified PWM pin timer number on Nucleo
        self.t = pyb.Timer(timer, freq = 50)
        ##Timer channel used to send PWM signal for specified Nucleo pin
        self.tch = self.t.channel(2,pyb.Timer.PWM, pin=pwm_pin)
    
    def pen_down(self):
        '''!
        @brief Send PWM signal moving the pen down in contact with the page
        '''
        self.tch.pulse_width_percent(5)
    
    def pen_up(self):
        '''!
        @brief Send PWM signal moving the pen up to no longer touch the page
        '''
        self.tch.pulse_width_percent(2)

    

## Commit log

2022-02-18 Model Uploads
    [2941 Mini Motor.SLDPRT, Belt.SLDPRT, Pencil Holder.SLDPRT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]
2022-03-14 Create Proto Pen Plotter.SLDASM
    [Proto Pen Plotter.SLDASM]
